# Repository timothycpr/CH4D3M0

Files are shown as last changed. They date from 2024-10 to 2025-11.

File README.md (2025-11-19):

# Focus_CHAdeMO

The software and information provided here relates to hazardous and potentially deadly uses. EV batteries and DC chargers can produce hundreds of Amps of current at more than 1000 Volts, which can literally vaporise body parts. As wiser man said "Not only will this kill you, it will hurt the whole time you're dying"

Anyone that utiizes this infomration/code must assume full responsibility for their actions and ensure prudent & safe operation. While good faith effort has been made to implement safety checks and fail-safes in code and hardware, I can in no way guarantee that using this is safe.

Similarly, modification of an EV to add after-market fast charging creates the same risks to people and property. Anyone implemeting any of these methods must assume full responsibility for their actions.

I will not be held liable for the actions of others relating to any use of this code, information or hardware.

With great power comes great responsibility - and 30-50kW is a *lot* of power.

-----------

Software and hardware specs to implement CHAdeMO fast charging on early model Ford Focus EVs

This hardware and software was originally developed and implemented by "Sefs" of the MyFocusElectic forums - building a home fast charger and a means to interface it with his vehicle.

After moving on to a Model 3 with much better range, the hardware was stripped from his 2012 Focus and eventually ended up in my 2012 Focus.

This project has two primary systems - the vehicle CHAdeMO interface and the charger-side management system.

In the vehicle CHAdeMO interface, an EVTV Due is spliced into the vehicle CANBus to send/receive/process CAN data frames. The data pins from the CHAdeMO plug are routed through a separate CANBus transceiver that converts them to a TTL data stream that is fed into the EVTV Due.

Data from these two systems is then used to control a CHAdeMO charging session, ultimately connecting the vehicle HVDC bus to that of the charger.

In total, the connection requires the following physical hardware:

  1 EVTV Due (http://store.evtv.me/proddetail.php?prod=EVTVDue2) ARM-based microcontroller with CAN Tranceiver

  1 EVAL-ADM3052EBZ (https://www.digikey.com/en/products/detail/analog-devices-inc/EVAL-ADM3052EBZ/2709315) Isolated CAN Transceiver

  1 HL-52S (https://www.newegg.com/p/285-0018-000E9?item=9SIA4W246U6059) Inverting Optocoupled 5V relays

  ~~1 PST-DC2012 (https://www.powerstream.com/DC3611.htm) or similarly capable, Fully Isolated DC/DC Converter with 12V output. (Original supply board was marked with a 5V model number - PST-DC2405 - but tested as 12V out)~~
  Using a double pole relay, one can switch the contactors to the vehicle 12V rather than driving them from a power supply on this board.

  1 12V SPDT relay and socket/harness (https://www.summitracing.com/parts/via-80237)

  2 3.3V optoisolators with breakouts (https://www.sparkfun.com/products/9118)

  2 Gigavac GX14BA Sealed Contactors (350A) (https://octopart.com/gx14ba-gigavac-24213166) 12V HVDC Normally open contactors

  1 CHAdeMO inlet (https://shop.quickchargepower.com/CHAdeMO-Inlets-YazInlet.htm) with harness

  1 Optional USB passthrough connector and USB A (host) to USB B (client)

  Resistors: +/-5%; 100 Ohm, 200 Ohm, 1 KOhm, two 15 KOhm.

After validating operation, all components have been consolidated onto a single shield, minus the HVDC contactors themselves. Components for re-inverting f/g/d1/d2 have been omitted and negated in code.

In addition to those signal path components, the following physical components are utilized

  1 plastic project box with grid insert

  1 replacement TCM cover (passthrough for HVDC wiring)

  6 crimp fit ring terminals ("Cable lugs"), 6 weatherproof passthroughs

  2 8-position terminal blocks

  1 7-wire weatherproof passthrough for CHAdeMO signal wiring

  1 4-wire or 2 2-wire weatherproof passthroughs for 12V/Ground/CANH/CANL

  ~30 crimp on fork terminals

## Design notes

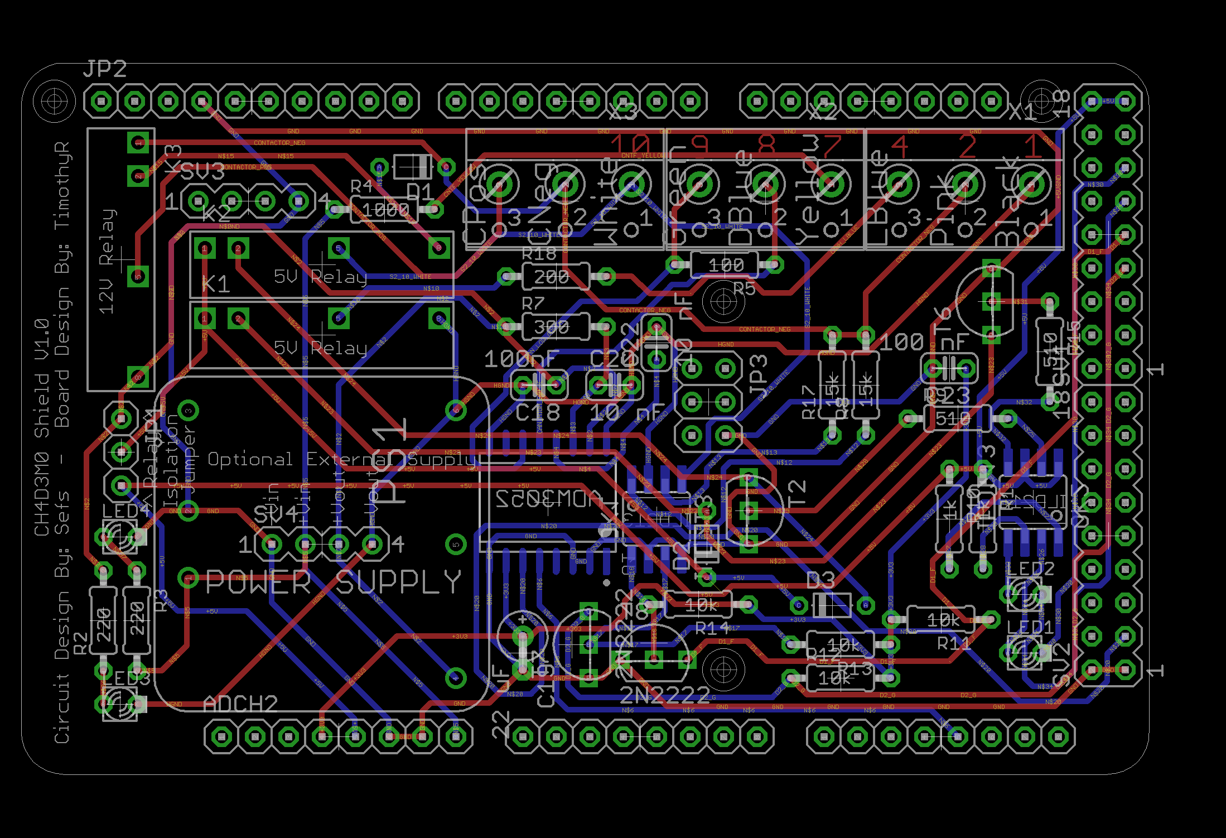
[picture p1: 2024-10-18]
CH4D3M0 Shield.png

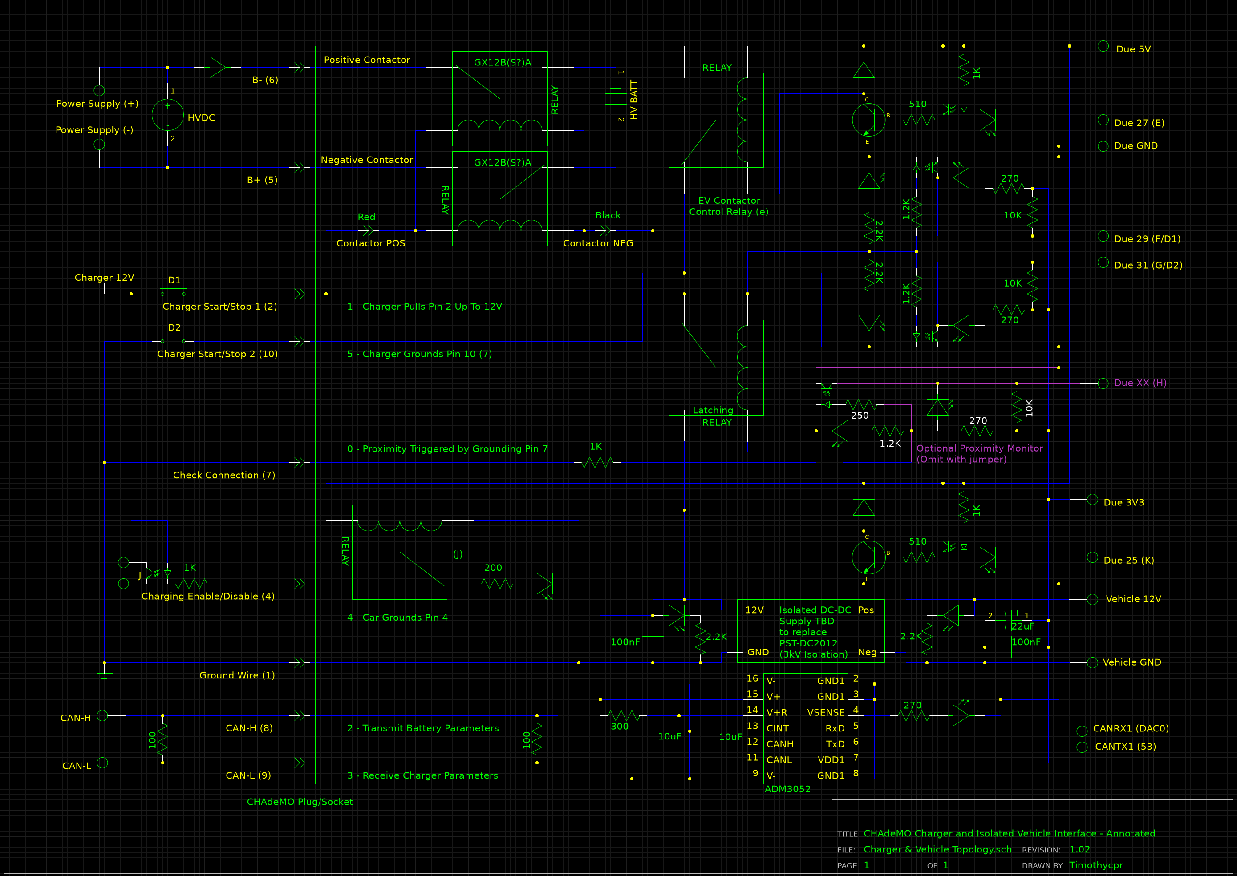
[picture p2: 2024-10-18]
Charger and Vehicle Topology.png

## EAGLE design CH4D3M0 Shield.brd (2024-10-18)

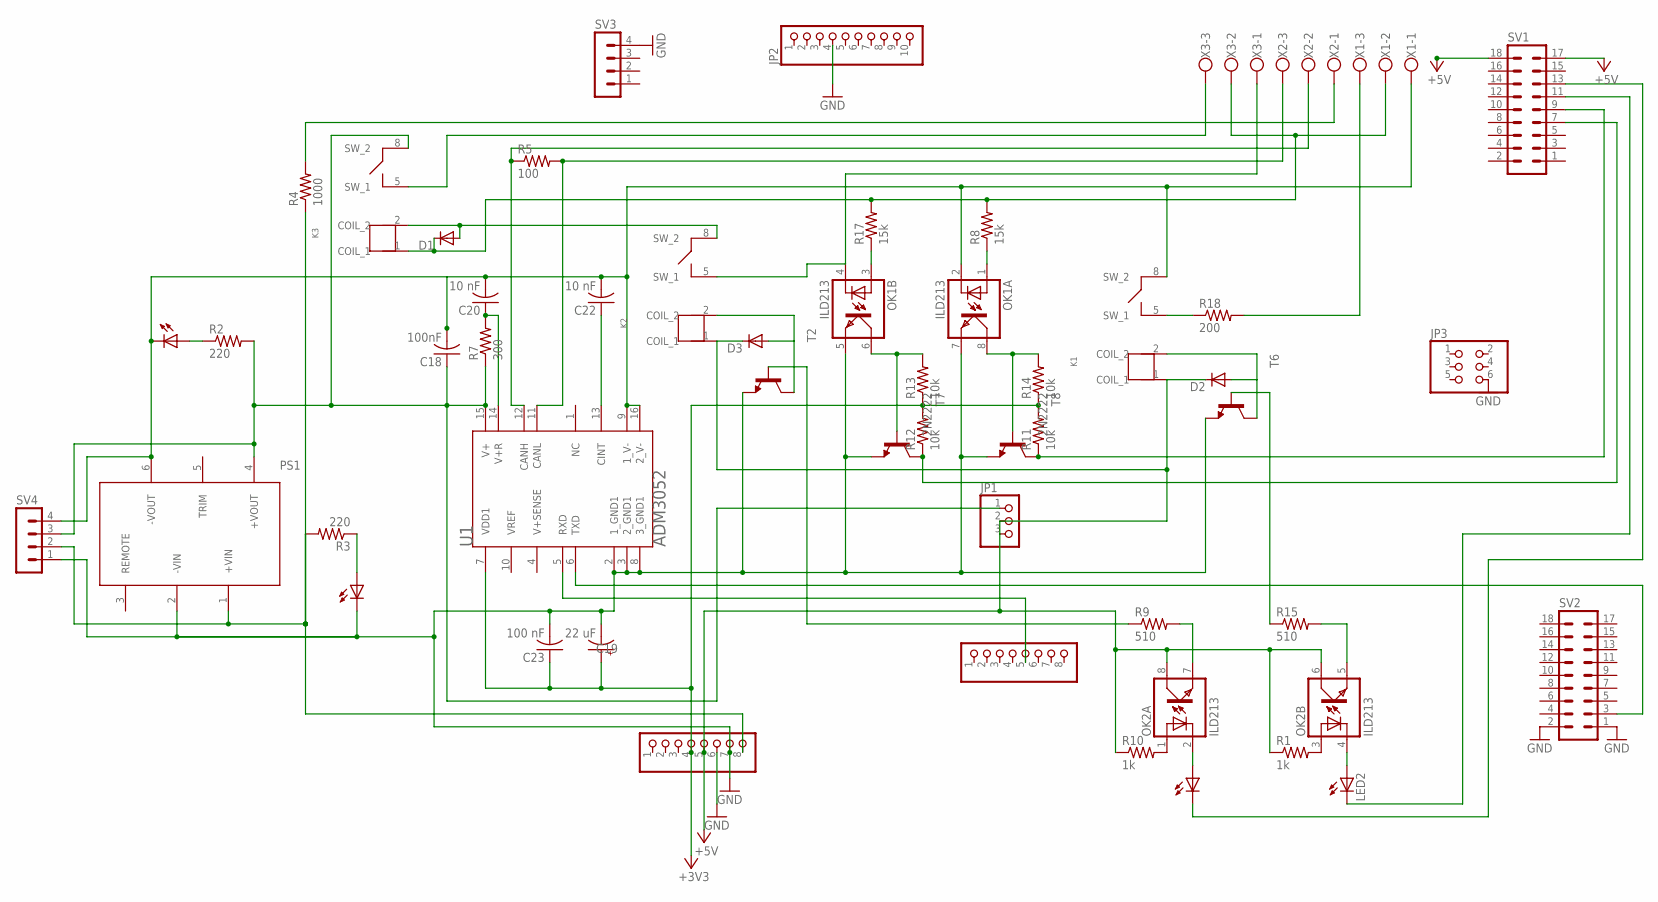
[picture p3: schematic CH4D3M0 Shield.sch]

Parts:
ADCH, ADCH2: PINHD-1X8; 1X08
C18: 100nF; C025-024X044
C19: 22 uF; E2,5RE
C20, C22: 10 nF; C025-024X044
C23: 100 nF; C025-024X044
D1, D2, D3: DIODE-D-5; D-5
JP1: PINHD-1X3; 1X03
JP2: PINHD-1X10; 1X10
JP3: PINHD-2X3; 2X03
K1, K2, K3: G6DN-1ATHROUGH_HOLE; G6DN-1A
LED1, LED2, LED3, LED4: LED_ELD260; LED_LD260
OK1, OK2: ILD213; SOIC08
PS1: JCMXXTHROUGH_HOLE; JCMXX
R1, R10: 1k; 0204/7
R2, R3: 220; 0204/7
R4: 1000; 0204/7
R5: 100; 0204/7
R7: 300; 0204/7
R8, R17: 15k; 0204/7
R9, R15: 510; 0204/7
R11, R12, R13, R14: 10k; 0204/7
R18: 200; 0204/7
SV1, SV2: MA09-2
SV3, SV4: MA04-1
T2, T6: BC547-NPN-TO92-CBE; TO92-CBE
T7, T8: 2N2222; TO92-EBC-OVAL
U1: ANALOG_DEVICES_INC_ADM3052ANALOG_DEVICES_INC_ADM3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; ANALOG_DEVICES_INC_ADM3052_0
X1, X2, X3: W237-103

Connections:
+3V3: ADCH2.4, C19.+, C23.1, R11.2, R12.2, R13.1, R14.1, U1.7 (VDD1)
+5V: ADCH2.5, D2.C, D3.C, JP1.2, JP1.3, K1.1 (COIL_1), K2.1 (COIL_1), OK2.6 (COL), OK2.8 (COL), R1.1, R10.1, SV1.17, SV1.18
CAN_HIGH_DBLUE: R5.1, U1.12 (CANH), X2.2
CAN_LOW_GREEN: R5.2, U1.11 (CANL), X2.3
CINH_LBLUE: R18.2, X1.3
CNTF_YELLOW: R4.2, X2.1
CONTACTOR_NEG: D1.C, K3.1 (COIL_1), R8.2, R17.2, X1.2, X3.2
CONTACTOR_POS: K3.5 (SW_1), X3.3
D1_F: R11.1, SV1.9, T8.C
D2_G: R12.1, SV1.7, T7.C
GND: ADCH2.6, ADCH2.7, C19.-, C23.2, JP2.4, JP3.6, LED4.K (C), OK1.5 (EMIT), OK1.7 (EMIT), PS1.2 (-VIN), SV2.1, SV2.2, SV3.4, SV4.1, T2.E, T6.E, T7.E, T8.E, U1.2 (1_GND1), U1.3 (2_GND1), U1.8 (3_GND1)
HGND: C18.2, C20.2, C22.2, K1.8 (SW_2), LED3.K (C), OK1.2 (C), PS1.6 (-VOUT), SV4.4, U1.9 (1_V-), U1.16 (2_V-), X1.1
unnamed: C18.1, JP1.1, K3.8 (SW_2), PS1.4 (+VOUT), R2.2, R7.1, SV4.3, U1.15 (V+)
unnamed: C20.1, R7.2, U1.14 (V+R)
unnamed: C22.1, U1.13 (CINT)
unnamed: ADCH2.8, PS1.1 (+VIN), R3.2, R4.1, SV4.2
unnamed: ADCH.5, U1.5 (RXD)
unnamed: K1.5 (SW_1), R18.1
unnamed: OK1.1 (A), R8.1
unnamed: OK1.3 (A), R17.1
unnamed: D1.A, K2.8 (SW_2), K3.2 (COIL_2)
unnamed: OK1.6 (COL), R13.2, T7.B
unnamed: OK1.8 (COL), R14.2, T8.B
unnamed: SV2.3, U1.6 (TXD)
unnamed: D2.A, K1.2 (COIL_2), T6.C
unnamed: D3.A, K2.2 (COIL_2), T2.C
unnamed: OK2.7 (EMIT), R9.2
unnamed: LED1.A, OK2.2 (C)
unnamed: OK2.1 (A), R10.2
unnamed: OK2.3 (A), R1.2
unnamed: R9.1, T2.B
unnamed: LED1.K (C), SV1.13
unnamed: R15.1, T6.B
unnamed: OK2.5 (EMIT), R15.2
unnamed: LED2.A, OK2.4 (C)
unnamed: LED2.K (C), SV1.11
unnamed: LED3.A, R2.1
unnamed: LED4.A, R3.1
S2_10_WHITE: K2.5 (SW_1), OK1.4 (C), X3.1

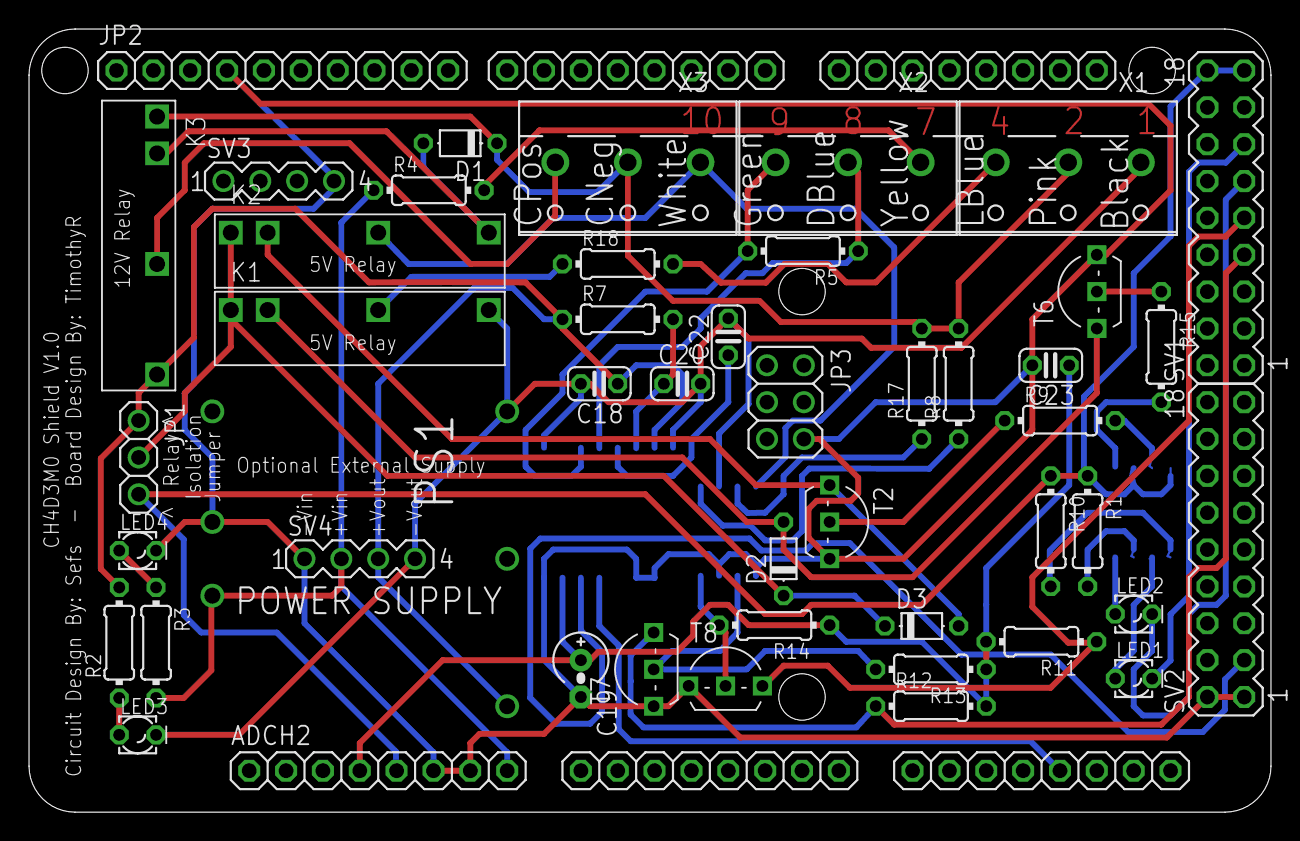
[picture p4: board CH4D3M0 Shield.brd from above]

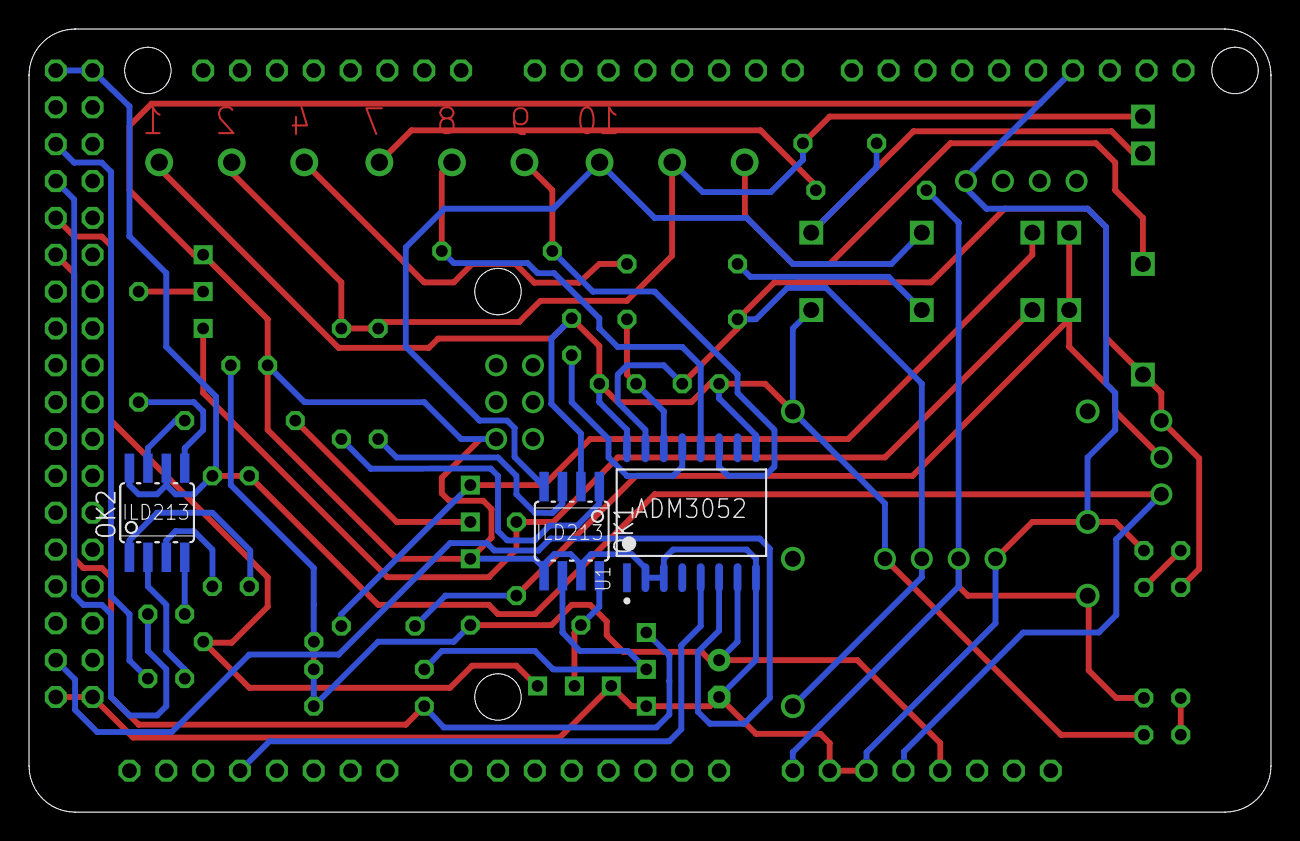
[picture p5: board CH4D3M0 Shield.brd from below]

Board: 2 copper layers, 85.6 x 54.0 mm, 54 parts (3 on the bottom side), 39 nets.

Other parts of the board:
ADCL: 1X08
COMMUNICATION: 1X08
PWML: 1X08

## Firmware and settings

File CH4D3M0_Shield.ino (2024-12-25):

/*
This code is forked from a private project of Sefs on the MyFocusElectric.com forum.

It is a work in progress and is provided with no warranty of any kind, under the licensing specified at https://github.com/timothycpr/CH4D3M0

It targets an Arduino Due with a SAM3X8E processor to operate CANBus monitoring on a separate thread from the charge state monitoring.

It originally paired to active low isolated relays and re-inverted optoisolators - and has been modified in parallel with prototyping of the CH4D3M0 shield

Depending on the topography of the circuit selected, it may require input or output controls to be inverted from the settings set below.
*/

#include <SPI.h>
#include <Arduino.h>
#include <due_can.h>
#include <due_wire.h>
#include "variant.h"
#include <Wire_EEPROM.h>
#include <Scheduler.h>

#define Serial SerialUSB

// TODO: Add proximity monitor, CANBus power monitor and CANBus power indicator

/*
Define classes and templates for future use
*/
template<class T> inline Print &operator <<(Print &obj, T arg) {  //Sets up Serial streaming in the format "Serial<<String;"
  obj.print(arg);
  return obj;
}

class Field {
  public:
    uint16_t msb;
    uint16_t bits;
    uint32_t data;
    char* fieldName;
};

class Msg {
  public:
    char* moduleName;
    uint16_t msgID;
    uint64_t msg;
    Field fields[16];
    uint8_t field_count;
};

class StringTable {
  public:
    Msg messages[32];
};

class EEPROMvariables {
  public:
    uint8_t CANdo; // Use Serial port if 2 (Default), CAN0 if 0 or CAN1 if 1
    char logfile[80];
    uint16_t transmitime = 0;
    boolean logger;
    uint32_t datarate = 125000; // lowest officially supported datarate for CANBus is 40kbit/sec
    uint8_t goodEEPROM;
    CAN_FRAME outFrame;
};

// Initialize variables
StringTable stringTable;
EEPROMvariables myVars;
uint16_t page = 475;
uint16_t dummy;
char cmdBuffer[100];
char logstring[200];
char logstring2[300] = "";
char logstringt[200];
char logstringt1[200];
char logstringc1[200];
char logstringts[200];
char msgBuff[100];
float Version = 1.10;
int ptrBuffer;
short logcycle = 0;
boolean handlingEvent, debug;
int seq = 0;
unsigned long lastrx = 0;
unsigned long lastactiverx = 0;
unsigned long howlongagorx = 0;
unsigned long howlonglastactiverx = 0;
int chacurrent = 0;
int chargestatus = 0;
float chacurrentf = 0;
float estchatimef = 0;
float seqf = 0;
float mincell = 0;
float maxcell = 0;
float deltacell = 0;
float batchadspl = 0;
float brakemode = 0;
float frictionbrake = 0;
float torquedelivered = 0;
int torquedeliveredint = 0;
float motorRPM = 0;
float MPH = 0;
float hbattchar = 0;
float brake = 0;
float acc = 0;
float pilot = 0;
float ampacity = 0;
float VAC = 0;
float AAC = 0;
float Hz = 0;
int sobdmdiagcycle = 0;
int sobdmtoggle = 0;
int becmdiagcycle = 0;
int becmtoggle = 1;
int socint = 0;
int maxchacurrent = 0;
int maxchatime = 0;
int zerocurrentwait = 0;
int estchatime = 0;
int maxchavoltage = 0;
int chastatusfault = 0;
int chastop = 0;
int vehstop = 0;
int brakeon = 0;
int chaenable = 0;
int compat = 0;
int incra = 0;
int wayup = 0;
int seq1start = 0;
int seq2start = 0;
// e, f, g & k pin assignments can likely be changed to almost any unused digital data pin on the Arduino Due, should they be in a more desirable location for shield layout.
int k = 25; // "Vehicle Ready" signal to charger (consider moving to 38)
int e = 27; // EV Contactor Relay e (consider moving to 40)
int f = 29; // Optoisolator to monitor for d1
int g = 31; // Optoisolator to monitor for d2
int d1 = 0; // d1 is monitored by the optoisolator for signal f
int d2 = 0; // d2 is monitored by the optoisolator for signal g
float hbattcoolin = 0;
float mcon = 0;
float hbattcurr = 0;
float currentandmcon = 0;
float ETE = 0;
float hbatttemp = 0;
float hbattvolt = 0;
float throttle = 0;
float pwrt = 0;
float hvac = 0;
CAN_FRAME inFrame;

void setup() { // Code to run as the initial configuration of the system

  Wire.begin(); // Initialize the wire library and join the I2C bus
  Serial.begin(115200); // opens serial port, sets serial data rate to 115200

  EEPROM.setWPPin(19); // Can't find good info on what WPPin is
  EEPROM.read(page, myVars); // Read the variable page from flash and into EEPROM variables
  if (myVars.goodEEPROM != 200)defaults(); // If the data isn't good, pull defaults from defaults function
  myVars.logger = false;

  initializeCAN(); // Yeah, that

//  Input and output values may need to be inverted depending on the hardware implementation utilized.
//  Optocouplers invert inputs by default, though some include an additional transistor that can invert the output back.
//  This code was written for relays with optocouplers that did not re-invert the signal, making them active-low control (activate when a control pin is tied to ground)
//  This code was written for re-inverting optocouplers monitoring inputs f and g and uses active high logic (d1 or d2 going "high" will create an output that is also "high")
//  Should circuit modifications be made, digital reads may need to be inverted by applying the NOT modifier (variable = !digitalRead(pin_num)) and writes should be replaced with their complementary value
  pinMode(k, OUTPUT); // 25 Relay control is active low
  pinMode(e, OUTPUT); // 27 Relay control is active low
  pinMode(f, INPUT);  // 29 2V+ (pullup to 3.3V) will read as 0/Low/False/Inactive with digital read (inverted)
  pinMode(g, INPUT);  // 31 2V+ (pullup to 3.3V) will read as 0/Low/False/Inactive with digital read (inverted)

  Scheduler.startLoop(ActiveDiagLoop); // Starts the ActiveDiagLoop in the background
}

void loop() { // The "main" loop of code to iterate indefinitely
  while (SerialUSB.available()) { // Start by checking serial
    serialEvent();
  }

//  Minimal parts config inverts these signals
  d1 = !digitalRead(f);  // Check for the state of pin 29
  d2 = !digitalRead(g);  // Check for the state of pin 31

  /* Tell me about them */
//  Serial<<"d1 = ";
//  Serial<<d1;
//  Serial<<"\n";
//  Serial<<"d2 = ";
//  Serial<<d2;
//  Serial<<"\n";

  if (d1 == 0 && d2 == 0) { // CHAdeMO pin 2 (f, pin 29) is floating and CHAdeMO pin 10 (g, pin 31) is floating
    seq = 0; // Charging sequence has not started at all yet
    seq1start = 0;  // All
    seq2start = 0;  // Variables
    chacurrent = 0; // Zero'd
    digitalWrite(k, HIGH); // True, relay open
    digitalWrite(e, HIGH); // True, relay open
  }
  else if (d1 == 1 && d2 == 0 && seq1start == 0) { // CHAdeMO pin 2 (f, pin 29) is has been connected to 12V and CHAdeMO pin 10 (g, pin 31) is floating
    seq = 1; // This signals state one of the charging sequence
    seq1start = 1; // Separate variables to be touched by different branches
  } // This triggers data collection on the car side CAN bus to be shared on the charger side CAN bus
  else if (d1 == 1 && d2 == 1 && seq2start == 0) { // CHAdeMO pin 2 (f, pin 29) is has been connected to 12V and CHAdeMO pin 10 (g, pin 31) is grounded
    seq = 3;
    seq2start = 1;
    digitalWrite(e, LOW); // False - Main Contactor On
  }
  else if (d1 == 0 && d2 == 1) { //Can be reduced to just the first d1/d2 == 0 being changed to d1 == 0 and deleting this block
    seq = 0;
    seq1start = 0;
    seq2start = 0;
    digitalWrite(k, HIGH); // True, relay open
    digitalWrite(e, HIGH); // True, relay open
    chacurrent = 0;
  }

  if (mcon == 0) {
    seq = 0;
//  Serial<<"mcon = ";
//  Serial<<mcon;
//  Serial<<"\n";
  }

  if (seq == 2 || seq == 3 || seq == 4) {
    estchatime = float (((-0.4 * maxchacurrent) + 77)) * (100 - socint) / 100 + 1; // Update estimated charge time with data captured from the active diag loop
  }
  if (seq == 0) {
    incra = 0;
//  Can1.disable();
    digitalWrite(k, HIGH); // True, relay open
    digitalWrite(e, HIGH); // True, relay open
    chacurrent = 0;
    maxchacurrent = 0;
    vehstop = 0;
    maxchatime = 60;
    estchatime = 0;
  }

  if (seq == 1) { // Transmit battery parameters, charging disabled
//  Can1.enable();
//  Compatibility Checks performed on data received on CAN1 through the handleFrame1

    myVars.outFrame.id = 0x100;
    myVars.outFrame.data.bytes[0] = 0x00;
    myVars.outFrame.data.bytes[1] = 0x00;
    myVars.outFrame.data.bytes[2] = 0x00;
    myVars.outFrame.data.bytes[3] = 0x00;
    myVars.outFrame.data.bytes[4] = 0x6C; //max battery voltage
    myVars.outFrame.data.bytes[5] = 0x01; //max battery voltage
    myVars.outFrame.data.bytes[6] = 0x64; //constant for SOC indication
    myVars.outFrame.data.bytes[7] = 0x00;
    sendCAN(myVars.CANdo);
    delay(1);

    myVars.outFrame.id = 0x101;
    myVars.outFrame.data.bytes[0] = 0x00;
    myVars.outFrame.data.bytes[1] = 0xFF; //max charging time by 10s
    myVars.outFrame.data.bytes[2] = maxchatime; //max charging time by 1 min
    myVars.outFrame.data.bytes[3] = estchatime; //estimated charging time
    myVars.outFrame.data.bytes[4] = 0x00;
    myVars.outFrame.data.bytes[5] = 0x00;
    myVars.outFrame.data.bytes[6] = 0x00;
    myVars.outFrame.data.bytes[7] = 0x00;
    sendCAN(myVars.CANdo);
    delay(1);

//  Vehicle permission not yet given, EV contactor still open
    myVars.outFrame.id = 0x102;
    myVars.outFrame.data.bytes[0] = 0x01; //version number
    myVars.outFrame.data.bytes[1] = 0x68; //target battery voltage
    myVars.outFrame.data.bytes[2] = 0x01; //target battery voltage
    myVars.outFrame.data.bytes[3] = 0x00; //requested current
    myVars.outFrame.data.bytes[4] = 0x00; //fault flag
    myVars.outFrame.data.bytes[5] = 0x08; //status flag (charging disabled, contact open)
    myVars.outFrame.data.bytes[6] = socint; //displayed SOC
    myVars.outFrame.data.bytes[7] = 0x00;
    sendCAN(myVars.CANdo);
    delay(1);

//  Compatability Checker

    if (compat == 1) {
      incra++;
    }
    else if (compat == 2) {
      seq = 0;
    }

    if (incra > 5 && incra < 10) {
      digitalWrite(k, LOW); // False - Vehicle grounds pin 4
    }
    else if (incra > 15) {
      seq = 2;
      incra = 0;
    }
  }
  else if (seq == 2) { // Transmit battery parameters, charging enabled, Vehicle permission given
  
    myVars.outFrame.id = 0x100;
    myVars.outFrame.data.bytes[0] = 0x00;
    myVars.outFrame.data.bytes[1] = 0x00;
    myVars.outFrame.data.bytes[2] = 0x00;
    myVars.outFrame.data.bytes[3] = 0x00;
    myVars.outFrame.data.bytes[4] = 0x6C; //max battery voltage
    myVars.outFrame.data.bytes[5] = 0x01; //max battery voltage
    myVars.outFrame.data.bytes[6] = 0x64; //constant for SOC indication
    myVars.outFrame.data.bytes[7] = 0x00;
    sendCAN(myVars.CANdo);
    delay(1);

    myVars.outFrame.id = 0x101;
    myVars.outFrame.data.bytes[0] = 0x00;
    myVars.outFrame.data.bytes[1] = 0xFF; //max charging time by 10s
    myVars.outFrame.data.bytes[2] = maxchatime; //max charging time by 1 min
    myVars.outFrame.data.bytes[3] = estchatime; //estimated charging time
    myVars.outFrame.data.bytes[4] = 0x00;
    myVars.outFrame.data.bytes[5] = 0x00;
    myVars.outFrame.data.bytes[6] = 0x00;
    myVars.outFrame.data.bytes[7] = 0x00;
    sendCAN(myVars.CANdo);
    delay(1);

//  Vehicle permission given, start isolation checks, EV contactor open still
    myVars.outFrame.id = 0x102;
    myVars.outFrame.data.bytes[0] = 0x01; //version number
    myVars.outFrame.data.bytes[1] = 0x68; //target battery voltage
    myVars.outFrame.data.bytes[2] = 0x01; //target battery voltage
    myVars.outFrame.data.bytes[3] = 0x00; //requested current
    myVars.outFrame.data.bytes[4] = 0x00; //fault flag
    myVars.outFrame.data.bytes[5] = 0x09; //status flag (charging enabled, contact open)
    myVars.outFrame.data.bytes[6] = socint; //displayed SOC
    myVars.outFrame.data.bytes[7] = 0x00;
    sendCAN(myVars.CANdo);
    delay(1);
    incra = 0;
  }

  else if (seq == 3) {  //Vehicle permission given, EV contactor has closed, wait to request current until 0x109.5.1 and indicate closed relay
    myVars.outFrame.id = 0x100;
    myVars.outFrame.data.bytes[0] = 0x00;
    myVars.outFrame.data.bytes[1] = 0x00;
    myVars.outFrame.data.bytes[2] = 0x00;
    myVars.outFrame.data.bytes[3] = 0x00;
    myVars.outFrame.data.bytes[4] = 0x6C; //max battery voltage
    myVars.outFrame.data.bytes[5] = 0x01; //max battery voltage
    myVars.outFrame.data.bytes[6] = 0x64; //constat for SOC indication
    myVars.outFrame.data.bytes[7] = 0x00;
    sendCAN(myVars.CANdo);
    delay(1);

    myVars.outFrame.id = 0x101;
    myVars.outFrame.data.bytes[0] = 0x00;
    myVars.outFrame.data.bytes[1] = 0xFF; //max charging time by 10s
    myVars.outFrame.data.bytes[2] = maxchatime; //max charging time by 1 min
    myVars.outFrame.data.bytes[3] = estchatime; //estimated charging time
    myVars.outFrame.data.bytes[4] = 0x00;
    myVars.outFrame.data.bytes[5] = 0x00;
    myVars.outFrame.data.bytes[6] = 0x00;
    myVars.outFrame.data.bytes[7] = 0x00;
    sendCAN(myVars.CANdo);
    delay(1);

    myVars.outFrame.id = 0x102;
    myVars.outFrame.data.bytes[0] = 0x01; //version number
    myVars.outFrame.data.bytes[1] = 0x68; //target battery voltage
    myVars.outFrame.data.bytes[2] = 0x01; //target battery voltage
    myVars.outFrame.data.bytes[3] = 0x00; //requested current
    myVars.outFrame.data.bytes[4] = 0x00; //fault flag
    myVars.outFrame.data.bytes[5] = 0x01; //status flag (charging enabled, contact closed)
    myVars.outFrame.data.bytes[6] = socint; //displayed SOC
    myVars.outFrame.data.bytes[7] = 0x00;
    sendCAN(myVars.CANdo);
    delay(1);
    incra++;
    if (incra > 10) {
      seq = 4;
      incra = 0;
      chacurrent = 1;
      wayup = 0;
      zerocurrentwait = 0;
    }
  }

  else if (seq == 4) {
    if (batchadspl > 99.5) { // Battery is full
      vehstop = 1;
    }
    myVars.outFrame.id = 0x100;
    myVars.outFrame.data.bytes[0] = 0x00;
    myVars.outFrame.data.bytes[1] = 0x00;
    myVars.outFrame.data.bytes[2] = 0x00;
    myVars.outFrame.data.bytes[3] = 0x00;
    myVars.outFrame.data.bytes[4] = 0x6C; //max battery voltage
    myVars.outFrame.data.bytes[5] = 0x01; //max battery voltage
    myVars.outFrame.data.bytes[6] = 0x64; //constat for SOC indication
    myVars.outFrame.data.bytes[7] = 0x00;
    sendCAN(myVars.CANdo);
    delay(1);

    myVars.outFrame.id = 0x101;
    myVars.outFrame.data.bytes[0] = 0x00;
    myVars.outFrame.data.bytes[1] = 0xFF; //max charging time by 10s
    myVars.outFrame.data.bytes[2] = maxchatime; //max charging time by 1 min
    myVars.outFrame.data.bytes[3] = estchatime; //estimated charging time
    myVars.outFrame.data.bytes[4] = 0x00;
    myVars.outFrame.data.bytes[5] = 0x00;
    myVars.outFrame.data.bytes[6] = 0x00;
    myVars.outFrame.data.bytes[7] = 0x00;
    sendCAN(myVars.CANdo);
    delay(1);

//  Vehicle permission given, EV contactor has closed, start requesting and indicate closed relay
    myVars.outFrame.id = 0x102;
    myVars.outFrame.data.bytes[0] = 0x01; //version number
    myVars.outFrame.data.bytes[1] = 0x68; //target battery voltage
    myVars.outFrame.data.bytes[2] = 0x01; //target battery voltage
    myVars.outFrame.data.bytes[3] = chacurrent; //requested current
    myVars.outFrame.data.bytes[4] = 0x00; //fault flag
    if ((chastop == 1 && incra > 20) || vehstop == 1) {
      myVars.outFrame.data.bytes[5] = 0x00; //status flag (charging enabled, contact closed)
      zerocurrentwait++;
    }
    else {
      myVars.outFrame.data.bytes[5] = 0x01; //status flag (charging enabled, contact closed)
      zerocurrentwait = 0;
    }
    myVars.outFrame.data.bytes[6] = socint; //displayed SOC
    myVars.outFrame.data.bytes[7] = 0x00;
    sendCAN(myVars.CANdo);
    delay(1);
    incra++;
    if (wayup == 0 && chaenable == 1) {
      if (chacurrent < maxchacurrent) {
        chacurrent = chacurrent + 2;
        if (chacurrent > maxchacurrent) {
          chacurrent = maxchacurrent;
        }
      }
      else {
        wayup = 1;
      }
    }

    if ((chastop == 1 && incra > 20) || vehstop == 1 ) {
      chacurrent = chacurrent - 20;
      if (chacurrent < 1) {
        chacurrent = 0;
      }
      wayup = 1;
      if (chacurrent == 0 && zerocurrentwait > 18) {
        seq = 5;
        chacurrent = 0;
        digitalWrite(k, HIGH); // True, relay open
//      digitalwrite(e,HIGH);
      }

    }
    if (hbattvolt >= 359 || maxcell > 4.15) {
      wayup = 1;
      if (chacurrent > 0) {
        chacurrent = chacurrent - 1;
      }
      /*else
      {
        chacurrent = 0;
        seq = 5;
        //digitalwrite(e,HIGH);
      }*/
    }
    incra = 0;
  }

  else if (seq == 5) {
    chacurrent = 0;
//  Permission Revoked, EV contactor has opened
    myVars.outFrame.id = 0x102;
    myVars.outFrame.data.bytes[0] = 0x01; //version number
    myVars.outFrame.data.bytes[1] = 0x68; //target battery voltage
    myVars.outFrame.data.bytes[2] = 0x01; //target battery voltage
    myVars.outFrame.data.bytes[3] = 0x00; //requested current
    myVars.outFrame.data.bytes[4] = 0x00; //fault flag
    if (chaenable == 0) {
      digitalWrite(e, LOW); // False, relay open
      myVars.outFrame.data.bytes[5] = 0x08; //status flag (charging enabled, contact closed)
      incra++;
    }
    else if (chaenable == 1) {
      myVars.outFrame.data.bytes[5] = 0x00; //status flag (charging enabled, contact closed)
    }
    myVars.outFrame.data.bytes[5] = 0x00; //status flag (charging enabled, contact closed)
    myVars.outFrame.data.bytes[6] = socint; //displayed SOC
    myVars.outFrame.data.bytes[7] = 0x00;
    sendCAN(myVars.CANdo);

    if (incra > 25) {
      seq = 0;
//    Can1.disable();
    }

  }
//  Brake mode
  if (frictionbrake > 0 && torquedelivered < -1) {
//  Blended
    brakemode = 2;
  }
  else if (frictionbrake > 0 && torquedelivered > -1) {
//  Friction
    brakemode = 3;
  }
  else if (frictionbrake == 0 && torquedelivered < -1) {
//  Regen
    brakemode = 1;
  }
  else if (frictionbrake == 0 && torquedelivered > -1) {
//  No Brake
    brakemode = 0;
  }

  chacurrentf = (float) chacurrent;
  seqf = (float) seq;

  estchatimef = (float) estchatime;
  sprintf(logstring2, "%.2f;%.2f;%.2f;%.2f;%.2f;%.2f;%.2f;%.2f;%.2f;%.2f;%.2f;%.2f;%.2f;%.2f;%.2f;%.2f;%.2f;%.2f;%.2f;%.2f;%.2f;%.2f;%.2f;%.2f;%.2f;%.2f;\n",
  batchadspl, hbattchar, hbattcoolin, mcon, hbattcurr, hbattvolt, ETE, hbatttemp, seqf, chacurrentf, torquedelivered,
  brakemode, estchatimef, motorRPM, MPH, throttle, brake, pwrt, acc, hvac, VAC, AAC, ampacity, Hz, mincell, maxcell);
//  Serial << logstring2;

  howlongagorx = (unsigned long) millis() - lastrx;
  howlonglastactiverx = (unsigned long) millis() - lastactiverx;

  if (howlongagorx > 500) {
    mincell = 0;
    maxcell = 0;
    deltacell = 0;
    batchadspl = 0;
    brakemode = 0;
    frictionbrake = 0;
    torquedelivered = 0;
    motorRPM = 0;
    MPH = 0;
    hbattchar = 0;
    becmtoggle = 0;
    hbattcoolin = 0;
    mcon = 0;
    hbattcurr = 0;
    currentandmcon = 0;
    ETE = 0;
    hbatttemp = 0;
    hbattvolt = 0;
    throttle = 0;
    pwrt = 0;
    hvac = 0;
  }
  if (howlonglastactiverx > 500) {
    mincell = 0;
    maxcell = 0;
    deltacell = 0;
    hbattvolt = 0;
  }
  if (seq == 1) {
    delay(97);
  }
  else {
    delay(100);
  }
}
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

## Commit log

2024-10-16 Add files via upload
    Annotated schematic of charger and vehicle CHAdeMO interfaces
    [Charger and Vehicle Topology.sch]
2024-10-18 Add files via upload
    Initial version of the shield board. Current power supply is incorrect
    [CH4D3M0 Shield.brd, CH4D3M0 Shield.sch]
2024-10-18 Add files via upload
    Tweaks of schematic - need to validate the resistor values
2024-10-18 Add files via upload
    Need to doublecheck all the read and write logic to make sure nothing is incorrectly inverted for the current circuit.
2024-10-18 Add files via upload
    App to monitor and display vehicle data during charging or operation. Appears to no longer work correctly in Windows 10.
2024-10-19 Update README.md
    Correcting power supply model number
2024-12-11 Add files via upload
    Initial upload of Arduino Due sketch. Work in progress, use at your own risk.
